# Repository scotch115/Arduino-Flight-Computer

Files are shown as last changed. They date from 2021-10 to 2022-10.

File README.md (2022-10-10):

# Arduino Telemetry

Arduino-based IMU telemetry system for model rockets. 

Phase 1: Build a basic Arduino project to learn basics of handling sensor data and developing on an MCU

Phase 2: Design and build a custom flight computer using accessible components and write flight-capable software.

Phase 3: Design and build a ground-control system to communicate with flight computer, handle launch sequence and startup, transmit data to and from the flight computer to a laptop.

Phase 4: Design and assemble the rocket airframe, mount the flight computer and Rotation Control System (RCS but not that kind ;P ), and test avionics and telemetry.

Phase 5: Build and test chute ejection system and determine required powder charge level.

Phase 6: Launch! 🚀

# Phase I - Research
## Temp Sensor PCB Design
### MK I
The MK I PCB was unfortunately unsuccessful, as I used the EasyEDA autoroute feature to try to solve track placement issues, however it did not take into account the possiblity of shorting the circuits, and neither did I, so my Arduino Nano blew a capacitor. Thankfully I have more, but this board was immediately decommissioned.

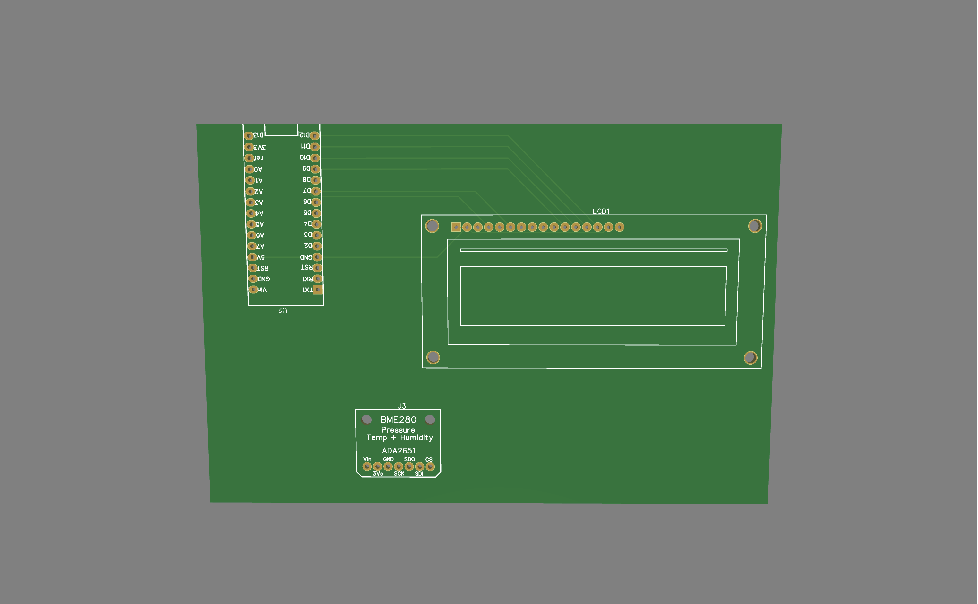
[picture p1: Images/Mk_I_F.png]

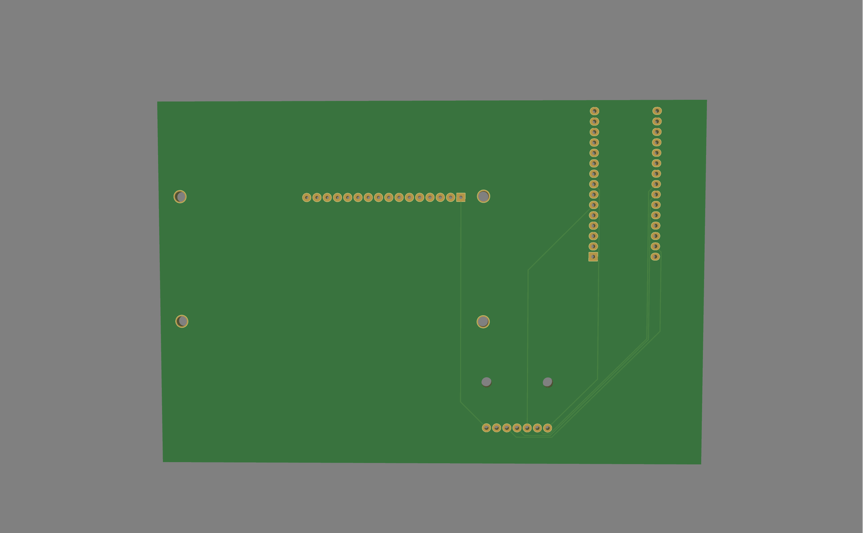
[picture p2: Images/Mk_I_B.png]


### MK II
The MK II PCB was carefully redesigned to improve upon the Mk I's failures by utilizing better component placement, built-in grounding pads, and hand-drawn track placement.

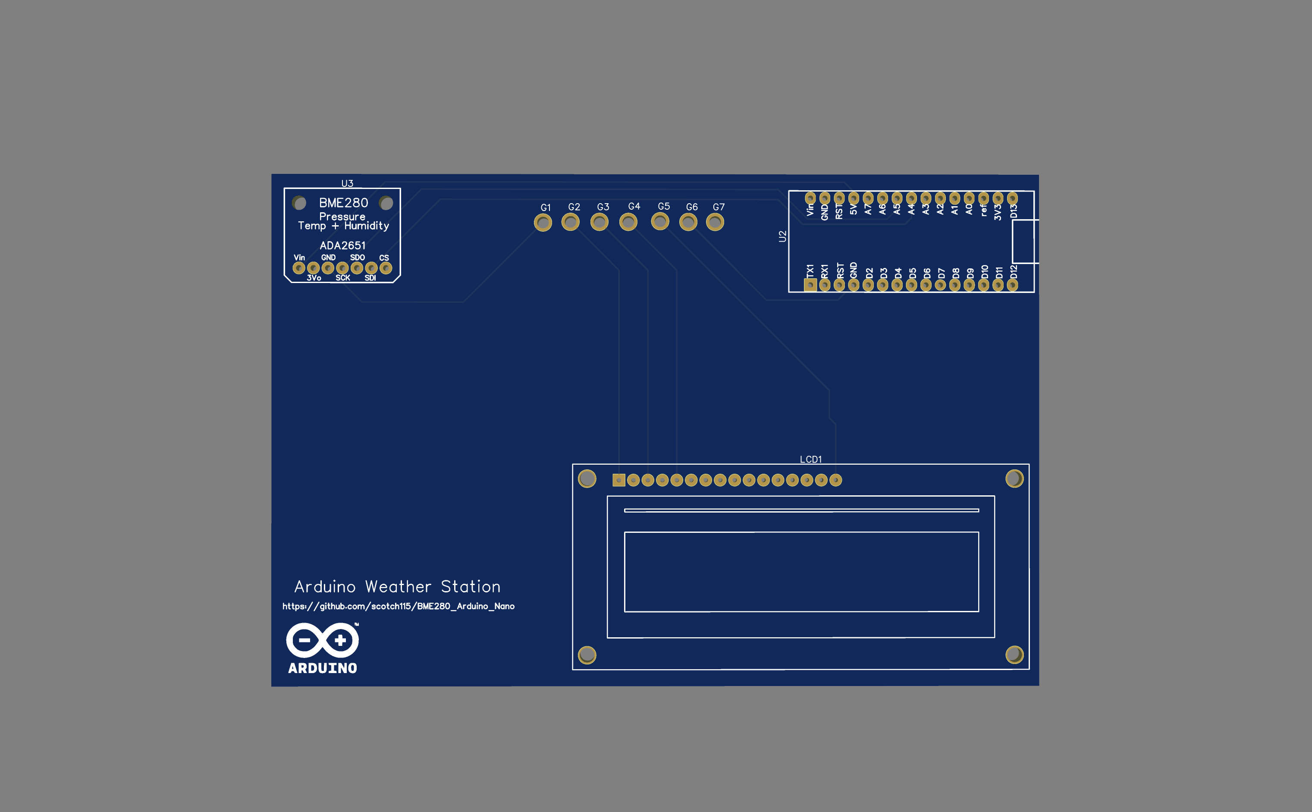
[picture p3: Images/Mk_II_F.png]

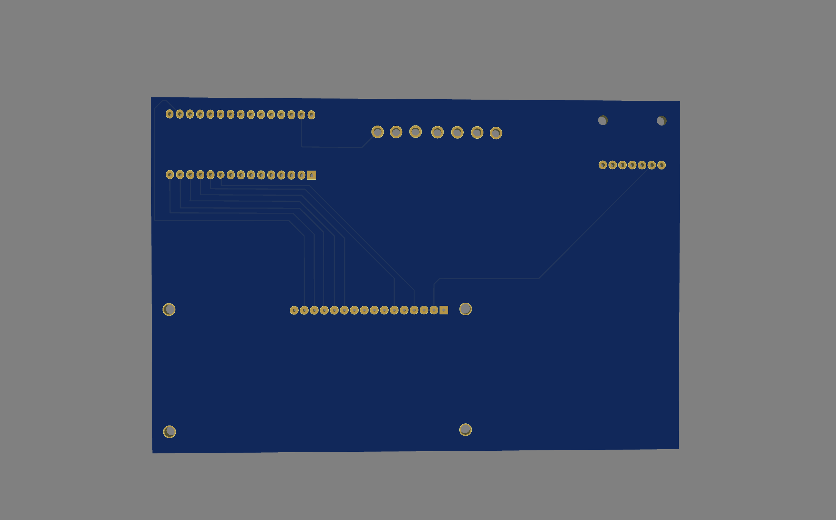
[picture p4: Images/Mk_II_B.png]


## Update:
Custom PCB worked after a slight modification to the electrical grounding system. Further research concluded that a "common ground" pin would have been more efficient and effective, than multiple pins.



# Phase II - Development
## Flight Computer
This is the assembled Mk.1 version of the flight computer, equipped with a barometer and IMU for tracking altitude, temperature, orientation, and velocity.




> UPDATE (MK. II)
>
> The flight computer has been upgraded to use the Adafruit Feather M0 with LoRa Radio @900Mhz, and the onboard IMU has been upgraded to the MPU 6050 with 6 DOF (and gyroscope!).

### MK.III
After working through various software iterations, the prototype board was complete and functional, but rather messy and utilized more patch wires than I preffered. Using the skills I learned from the PCB design in Phase 1, I began designing a new flight computer PCB, with the intent of using the same core components from the prototype board, allowing an easy transition of functionality, and requiring litte to no software logic changes. The Blep flight computer was developed, and serves as a major improvement in terms of efficiency, durability, and technological advancement. Having learned from my mistakes with the Phase 1 power management, I introduced a single common ground via on the PCB, as well as an entire "ground plane" within the layers of the PCB to ensure that all of the routes on the front and back of the board share a truly **common** ground.



# Phase III - Ground Control
## Mk. I
The AirLift Wi-Fi Co-Processor on both the Adalogger and Metro are able to successfully communicate with the Node-Red server, to send sensor data over UDP for collection and assimilation. The Node-Red dashboard is configured to not only build graphs in real-time, but also saves the data as it is received to a JSON file. 

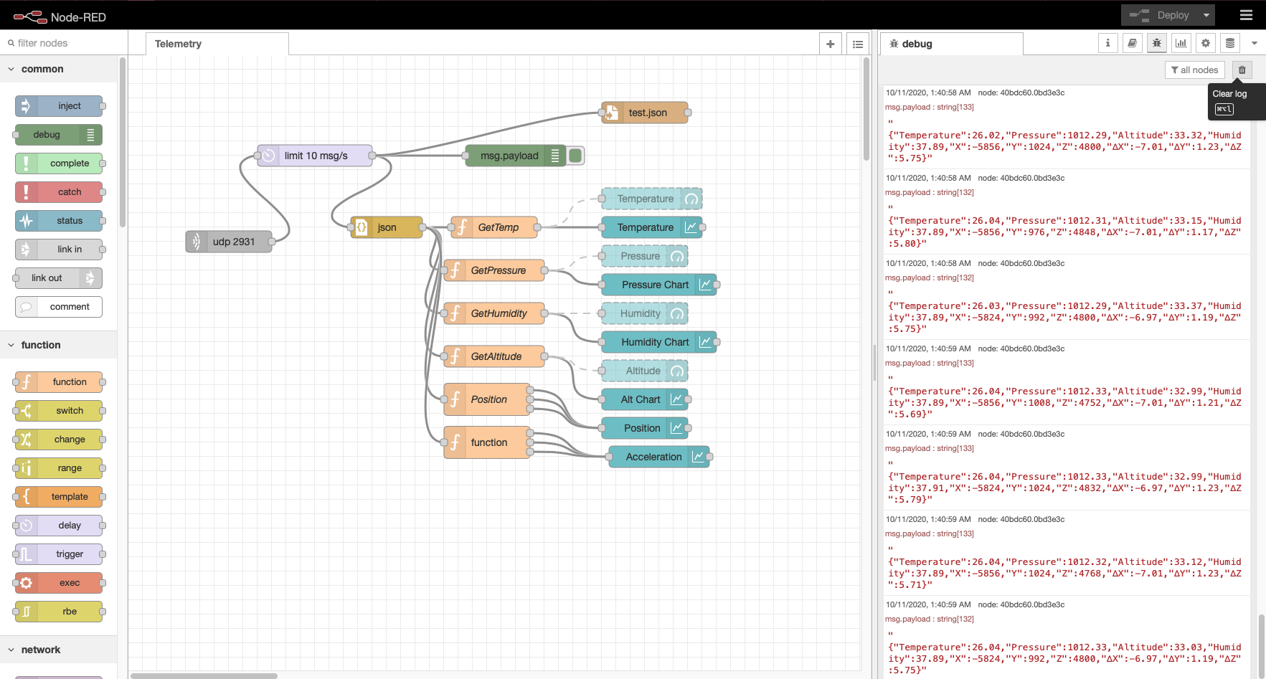
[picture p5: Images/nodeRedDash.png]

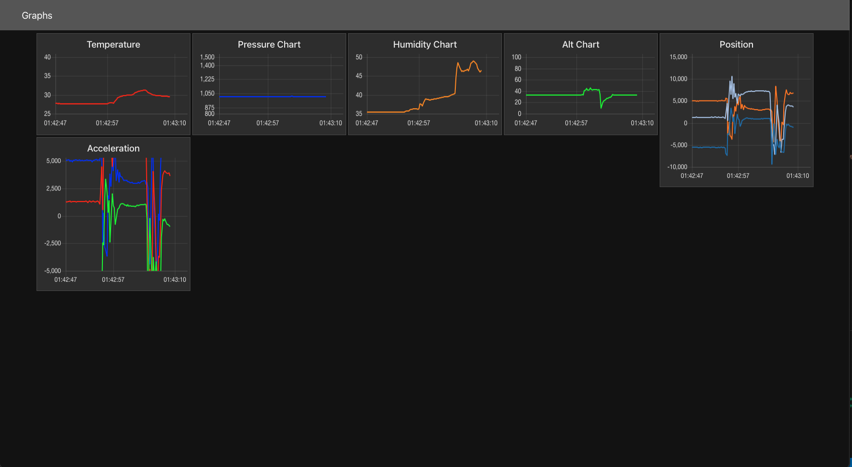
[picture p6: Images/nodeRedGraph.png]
  

## Mk. II
When the flight computer software is complete, the ground control system will be updated. Now that the onboard telemtry has shifted to use 900Mhz radio, the communication with the rocket will also be updated to use radio, and the data received by the ground control computer will be sent to a new server for analysis and logging. The new data analysis server utilizes Serial Studio instead of node-red, which is significantly more robust and efficient when dealing with high-speed data input, and doesn't suffer from the read/write operations to graphs, but still provides a JSON file as output for post-launch analysis. The primary MCU for the ground control computer will be a Teensy 3.2, connected to a LoRa Featherwing using the Teensy-Feather adapter board. 

# Phase IV - Rocket Design and Construction 
> ~~Currently doing research and teaching myself rocket mechanics to design and build a stable, efficient rocket.~~  
> UPDATE (9/2022): The rocket airframe is being designed simultaneous with Phase II, and rudimentary schematics will be included in this repo for future use. Old PCB schematics have been scrubbed from the project, as they are no longer relevant or necessary, and have been replaced by the Blep flight computer PCB files. Airframe construction will likely begin in the order planned.

# Phase V - Chute Ejection System
> Development still in progress...

# Phase VI - Launch!
> Development still in progress...

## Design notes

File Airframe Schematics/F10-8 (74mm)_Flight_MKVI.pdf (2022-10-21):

## Rocket Design

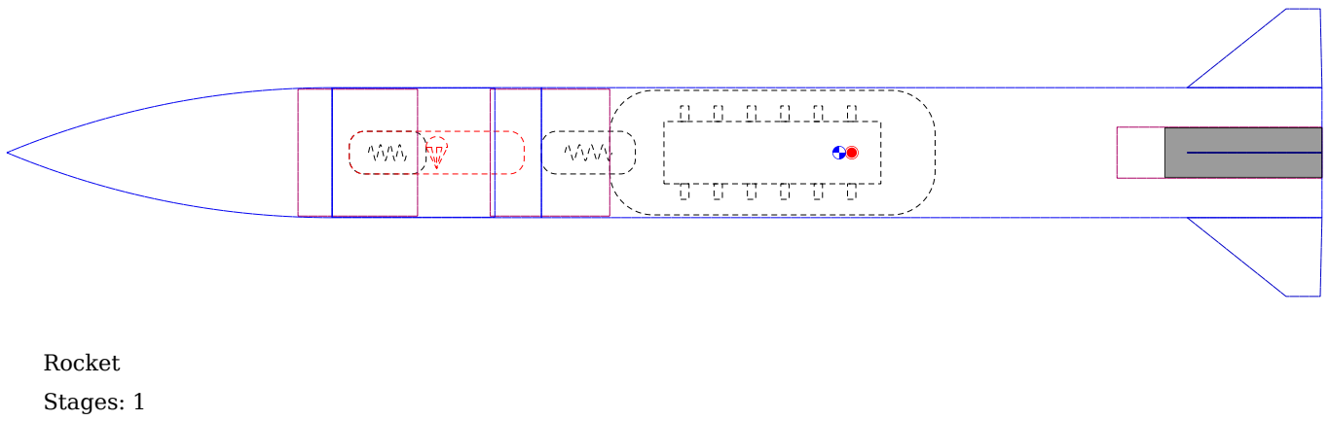
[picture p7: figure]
Rocket; Stages: 1

F10-8

Mass (with motor): 447 g

Stability: 0.097 cal

CG: 48.7 cm

CP: 49.5 cm

Altitude | 513 m
Flight Time | 60.1 s

Time to Apogee 12.2 s

Optimum Delay 5.1 s

Velocity off Pad 9.79 m/s

Max Velocity | 67.3 m/s
Velocity at Deployment | 3.26 m/s

Landing Velocity 10.7 m/s

Motor | Avg Thrust | Burn Time | Max Thrust | Total Impulse | Thrust to Wt | Motor Wt | Size
F10 | 10.9 N | 7.02 s | 28.2 N | 76.3 Ns | 2.48:1 | 40.7 g | 29/92 mm

## Parts Detail

Sustainer

Nose cone | [material:[mate
rial:polystyrene
PS]]

(1 g/cm³)

Ogive | Len: 19 cm | Mass: 92.7 g
Body tube | Cardboard

(0.68 g/cm³)

Diain 7.44 cm
Diaout 7.62 cm
| Len: 12.2 cm | Mass: 17.7 g
Tube coupler | Cardboard

(0.68 g/cm³)

Diain | 7.44 cm
Diaout 7.44 cm | Len: 7 cm | Mass: 0 g
Parachute | Ripstop nylon

(67 g/m²)

Diaout 30 cm | Len: 10.2 cm | Mass: 7.98 g
Shroud Lines | Elastic cord
(round 2 mm,
1/16 in)

(1.8 g/m)

Lines: 6 | Len: 30 cm
Shock cord | Kevlar thread
800 (1.1 mm,
3/64 in)

(0.992 g/m)

Len: 40 cm | Mass: 0.397 g
Body tube | Cardboard

(0.68 g/cm³)

Diain 7.44 cm
Diaout 7.62 cm
Len: 45.7 cm | Mass: 66.2 g
Tube coupler | Cardboard

(0.68 g/cm³)

Diain 7.44 cm
Diaout 7.44 cm
Len: 7 cm | Mass: 0 g
Flight Computer | Diaout 7.3 cm | Mass: 96 g
Inner Tube | Cardboard

(0.68 g/cm³)

Diain | 2.9 cm
| Diaout 2.99 cm
Len: 12 cm | Mass: 3.4 g
Trapezoidal fin set (4) | PLA

(1.25 g/cm³)

| Thick: 0.8 cm | Mass: 77.7 g
Shock cord | Kevlar thread
800 (1.1 mm,
3/64 in)

(0.992 g/m)

Len: 40 cm Mass: 0.397 g

## Trapezoidal fin set

## Trapezoidal fin set

## Trapezoidal fin set

## Trapezoidal fin set

## in cm

cm
in

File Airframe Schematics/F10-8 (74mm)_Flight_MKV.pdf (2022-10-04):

## Rocket Design

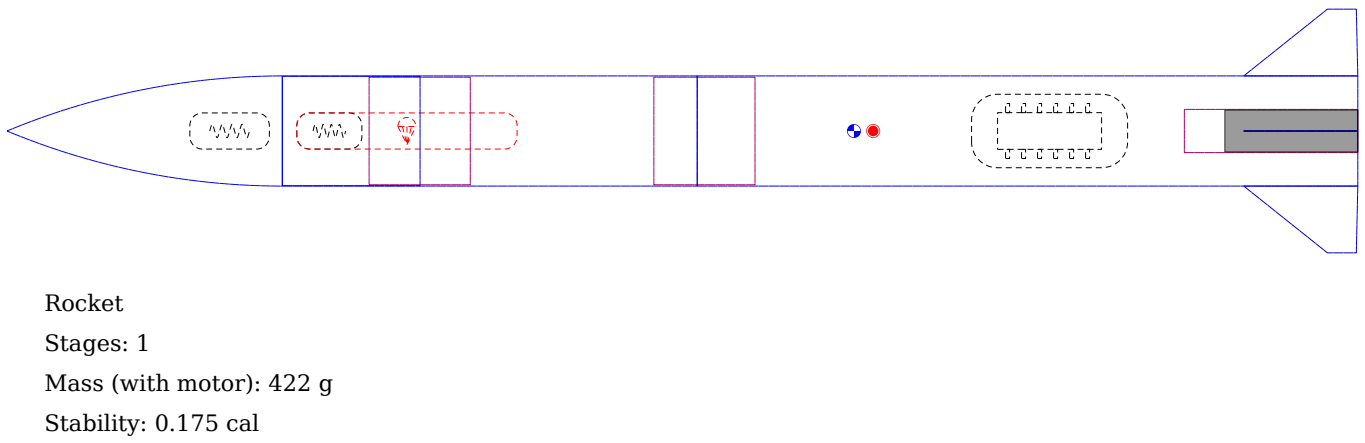
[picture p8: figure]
Rocket; Stages: 1; Mass (with motor): 422 g; Stability: 0.175 cal

F10-8

CG: 58.6 cm

CP: 59.9 cm

Altitude | 520 m
Flight Time | 62.2 s

Time to Apogee 12.1 s

Optimum Delay 5 s

Velocity off Pad 10.5 m/s

Max Velocity | 68.3 m/s
Velocity at Deployment | 5.24 m/s

Landing Velocity 10.4 m/s

Motor | Avg Thrust | Burn Time | Max Thrust | Total Impulse | Thrust to Wt | Motor Wt | Size
F10 | 10.9 N | 7.02 s | 28.2 N | 76.3 Ns | 2.62:1 | 40.7 g | 29/92 mm

## Parts Detail

Sustainer

Nose cone | [material:[mate
rial:polystyrene
PS]]

(1 g/cm³)

Ogive | Len: 19 cm | Mass: 92.7 g
Body tube | Cardboard

(0.68 g/cm³)

Diain 7.44 cm
Diaout 7.62 cm
| Len: 28.7 cm | Mass: 41.6 g
Tube coupler | Cardboard

(0.68 g/cm³)

Diain | 7.44 cm
Diaout 7.44 cm | Len: 7 cm | Mass: 0 g
Parachute | Ripstop nylon

(67 g/m²)

Diaout 30 cm | Len: 15.2 cm | Mass: 7.98 g
Shroud Lines | Elastic cord
(round 2 mm,
1/16 in)

(1.8 g/m)

Lines: 6 | Len: 30 cm
Shock cord | Elastic cord
(round 2 mm,
1/16 in)

(1.8 g/m)

Len: 40 cm | Mass: 0.72 g
Body tube | Cardboard

(0.68 g/cm³)

Diain 7.44 cm
Diaout 7.62 cm
Len: 45.7 cm | Mass: 66.2 g
Tube coupler | Cardboard

(0.68 g/cm³)

Diain 7.44 cm
Diaout 7.44 cm
Len: 7 cm | Mass: 0 g
Flight Computer | Diaout 5.08 cm | Mass: 96 g
Inner Tube | Cardboard

(0.68 g/cm³)

Diain | 2.9 cm
| Diaout 2.99 cm
Len: 12 cm | Mass: 3.4 g
Trapezoidal fin set (4) | PLA

(1.25 g/cm³)

| Thick: 0.3 cm | Mass: 29.1 g
Shock cord | Elastic cord
(round 2 mm,
1/16 in)

(1.8 g/m)

Len: 40 cm Mass: 0.72 g

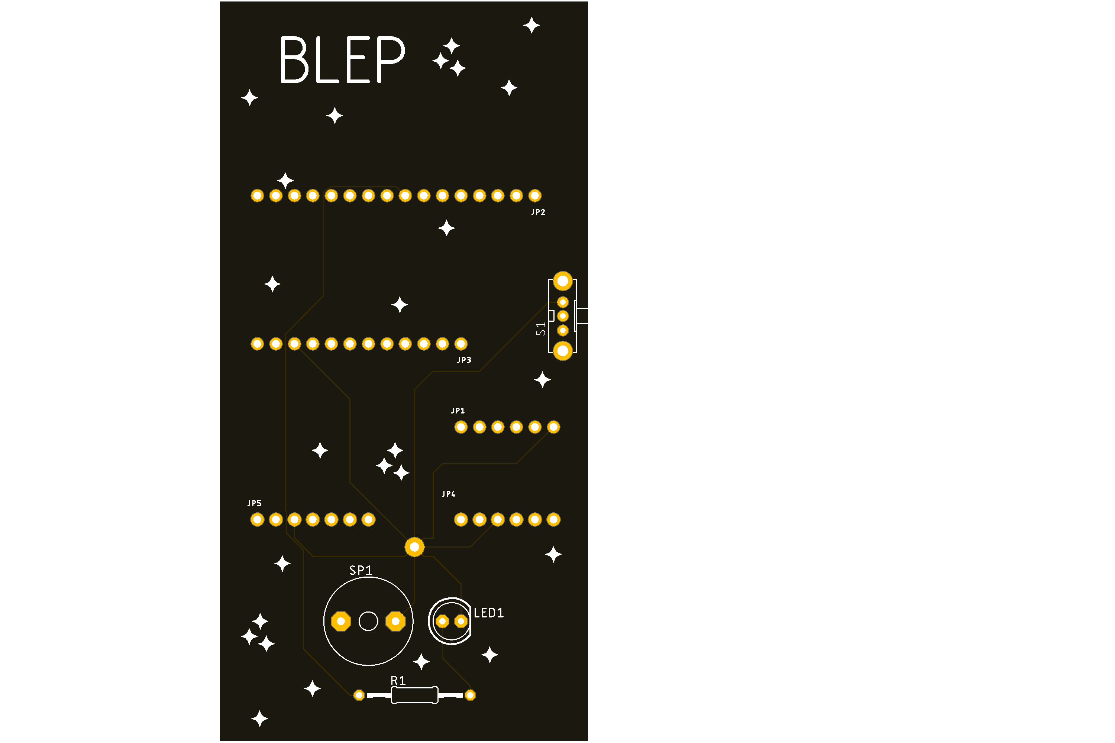
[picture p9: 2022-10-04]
Schematics/PCB Design Files/FlightComputer-PCB.png

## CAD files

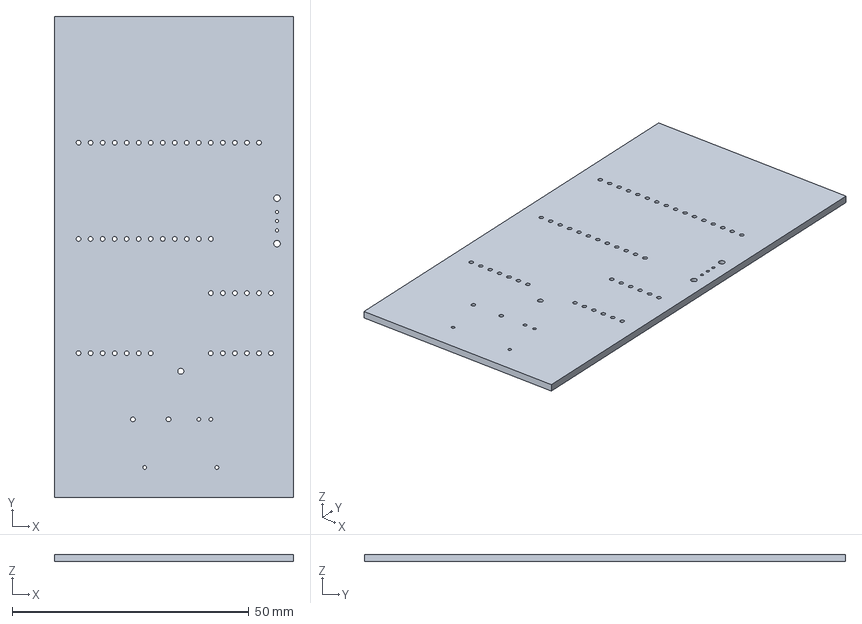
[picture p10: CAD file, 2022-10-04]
Schematics/PCB Design Files/FlightComputer v6.step
50.5 x 101.6 x 1.57 mm

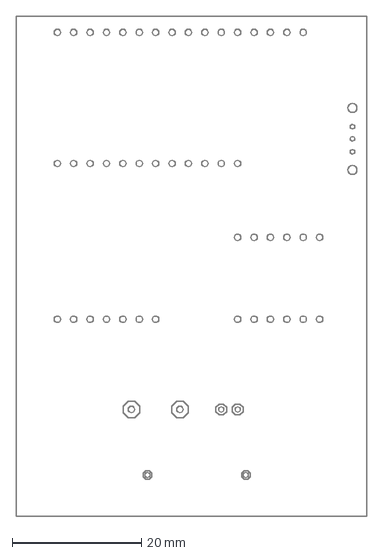
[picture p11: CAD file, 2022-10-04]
Schematics/PCB Design Files/FlightComputer.dxf
54.3 x 77.5 mm

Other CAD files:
Schematics/Technical Drawings/Servo Mount.dwg
Schematics/Technical Drawings/Avionics Payload Mount.dwg
Schematics/Technical Drawings/Sled Plate.dwg

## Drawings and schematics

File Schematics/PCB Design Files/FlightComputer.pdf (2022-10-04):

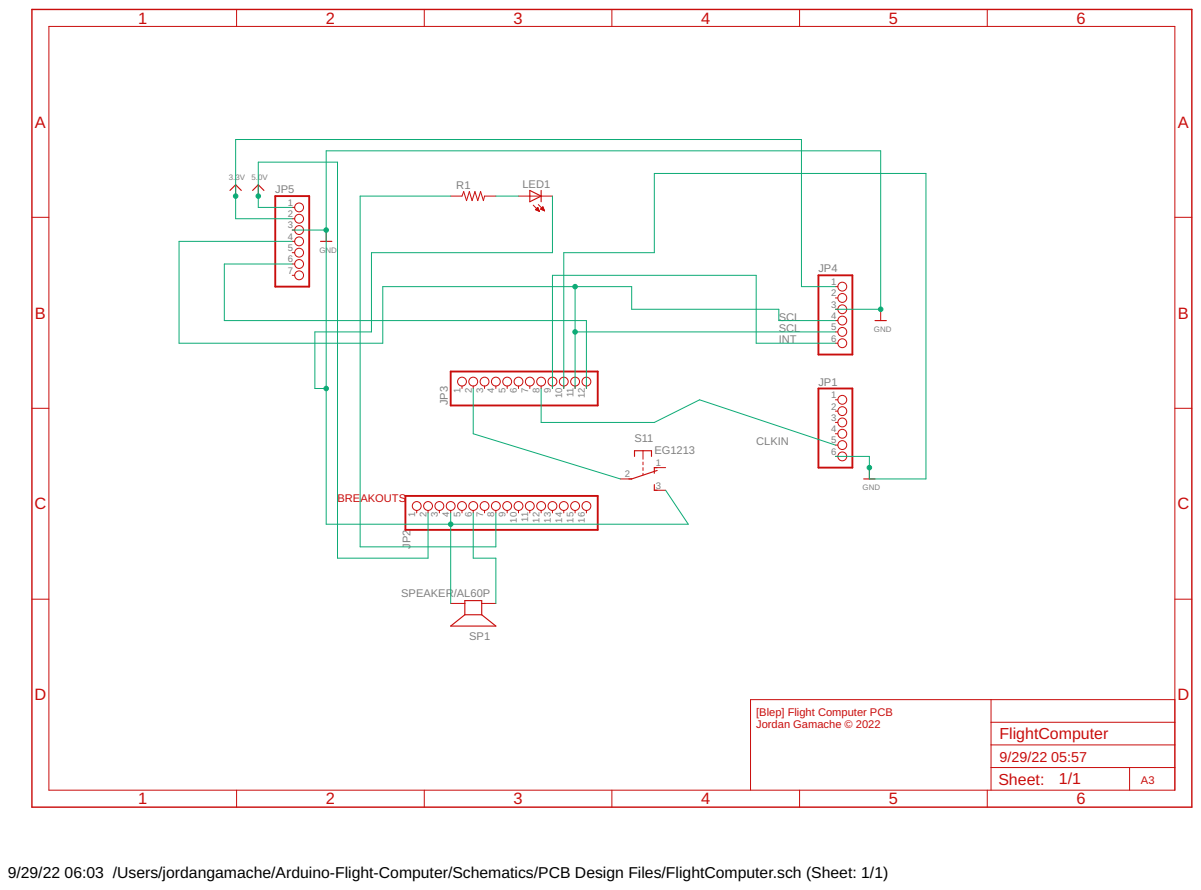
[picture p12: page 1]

[Blep] Flight Computer PCB Jordan Gamache © 2022

Sheet: 1/1 | A3

9/29/22 06:03 /Users/jordangamache/Arduino-Flight-Computer/Schematics/PCB Design Files/FlightComputer.sch (Sheet: 1/1)

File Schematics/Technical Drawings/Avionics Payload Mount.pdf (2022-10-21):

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

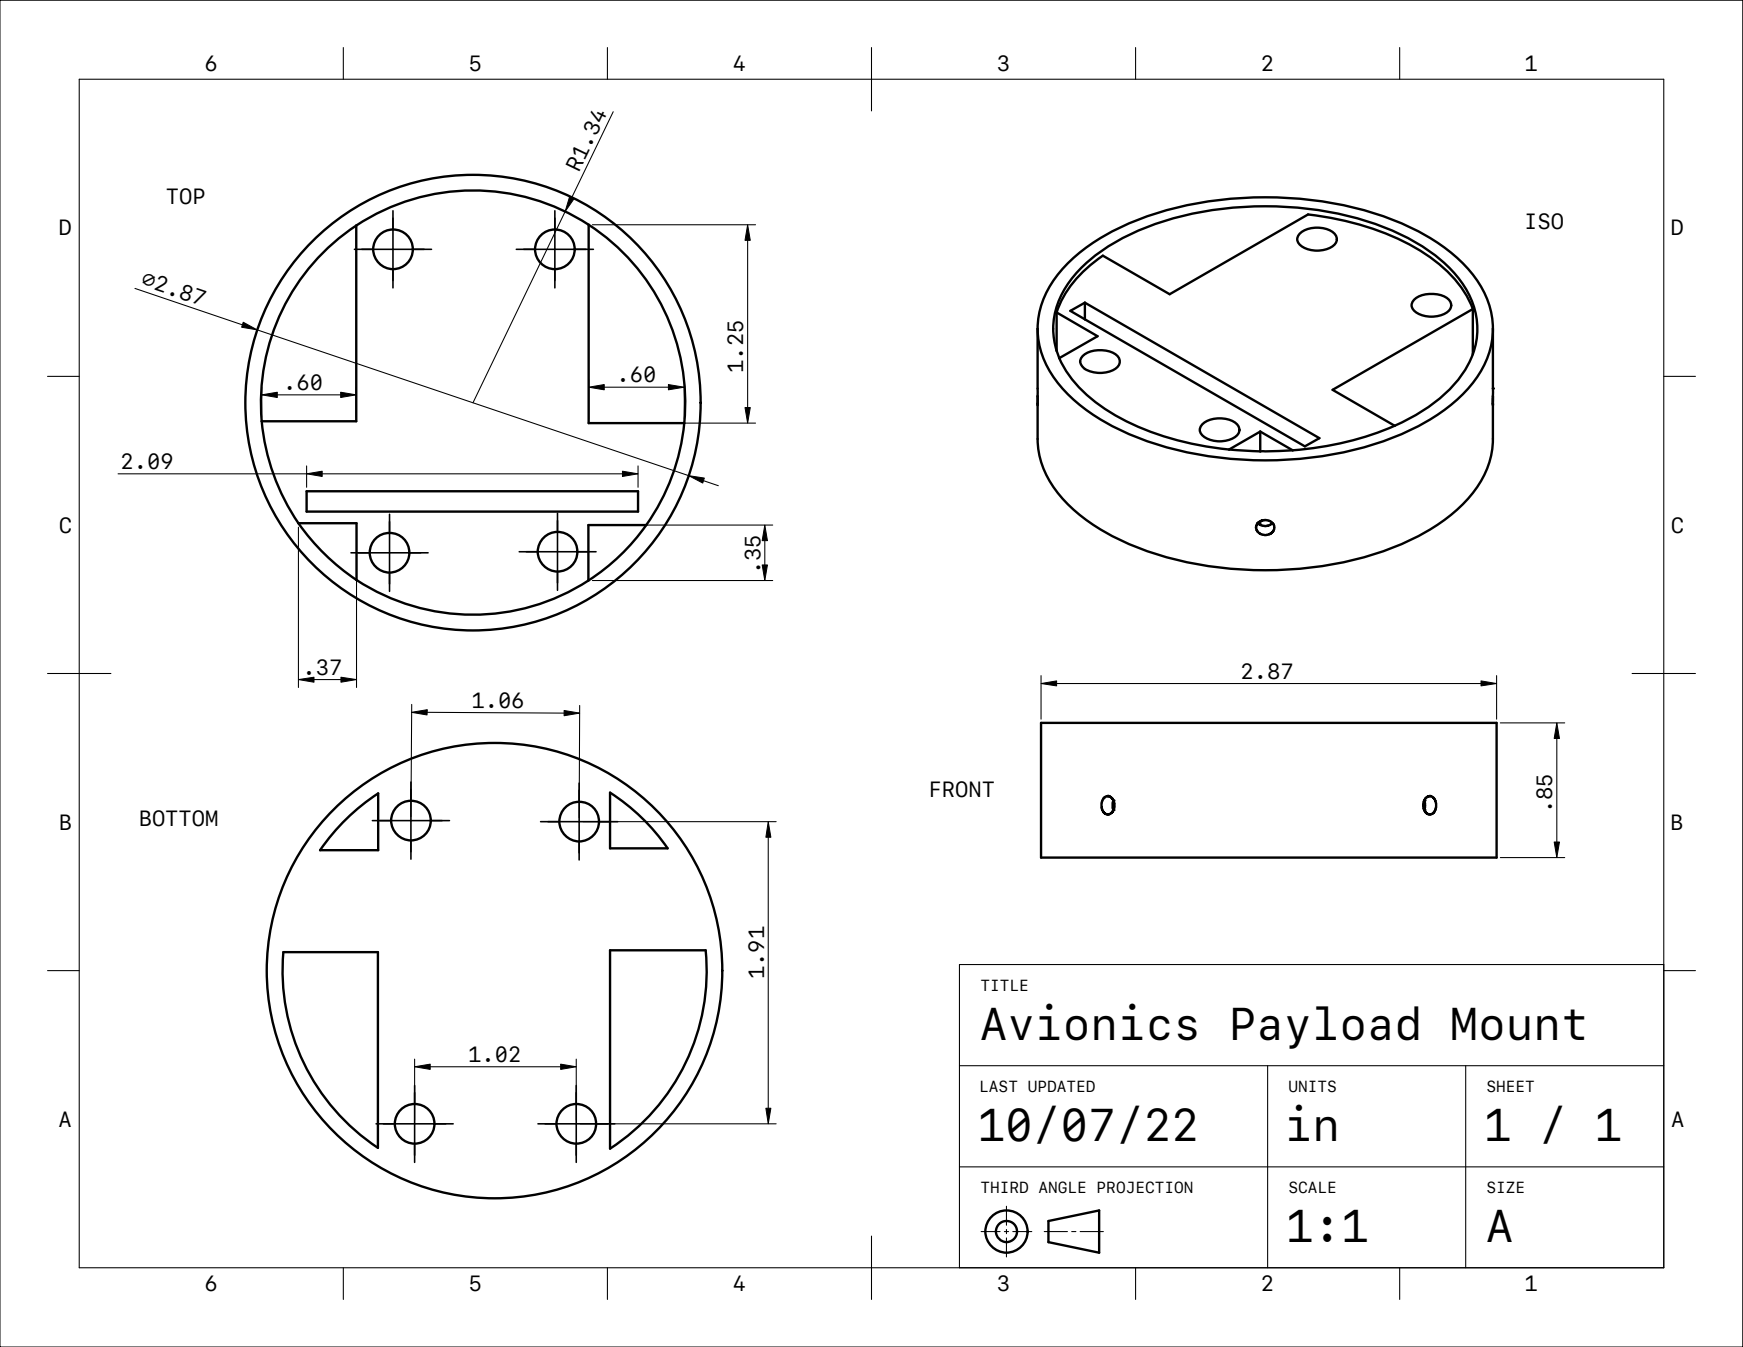
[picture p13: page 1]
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

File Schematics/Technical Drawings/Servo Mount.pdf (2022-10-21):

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

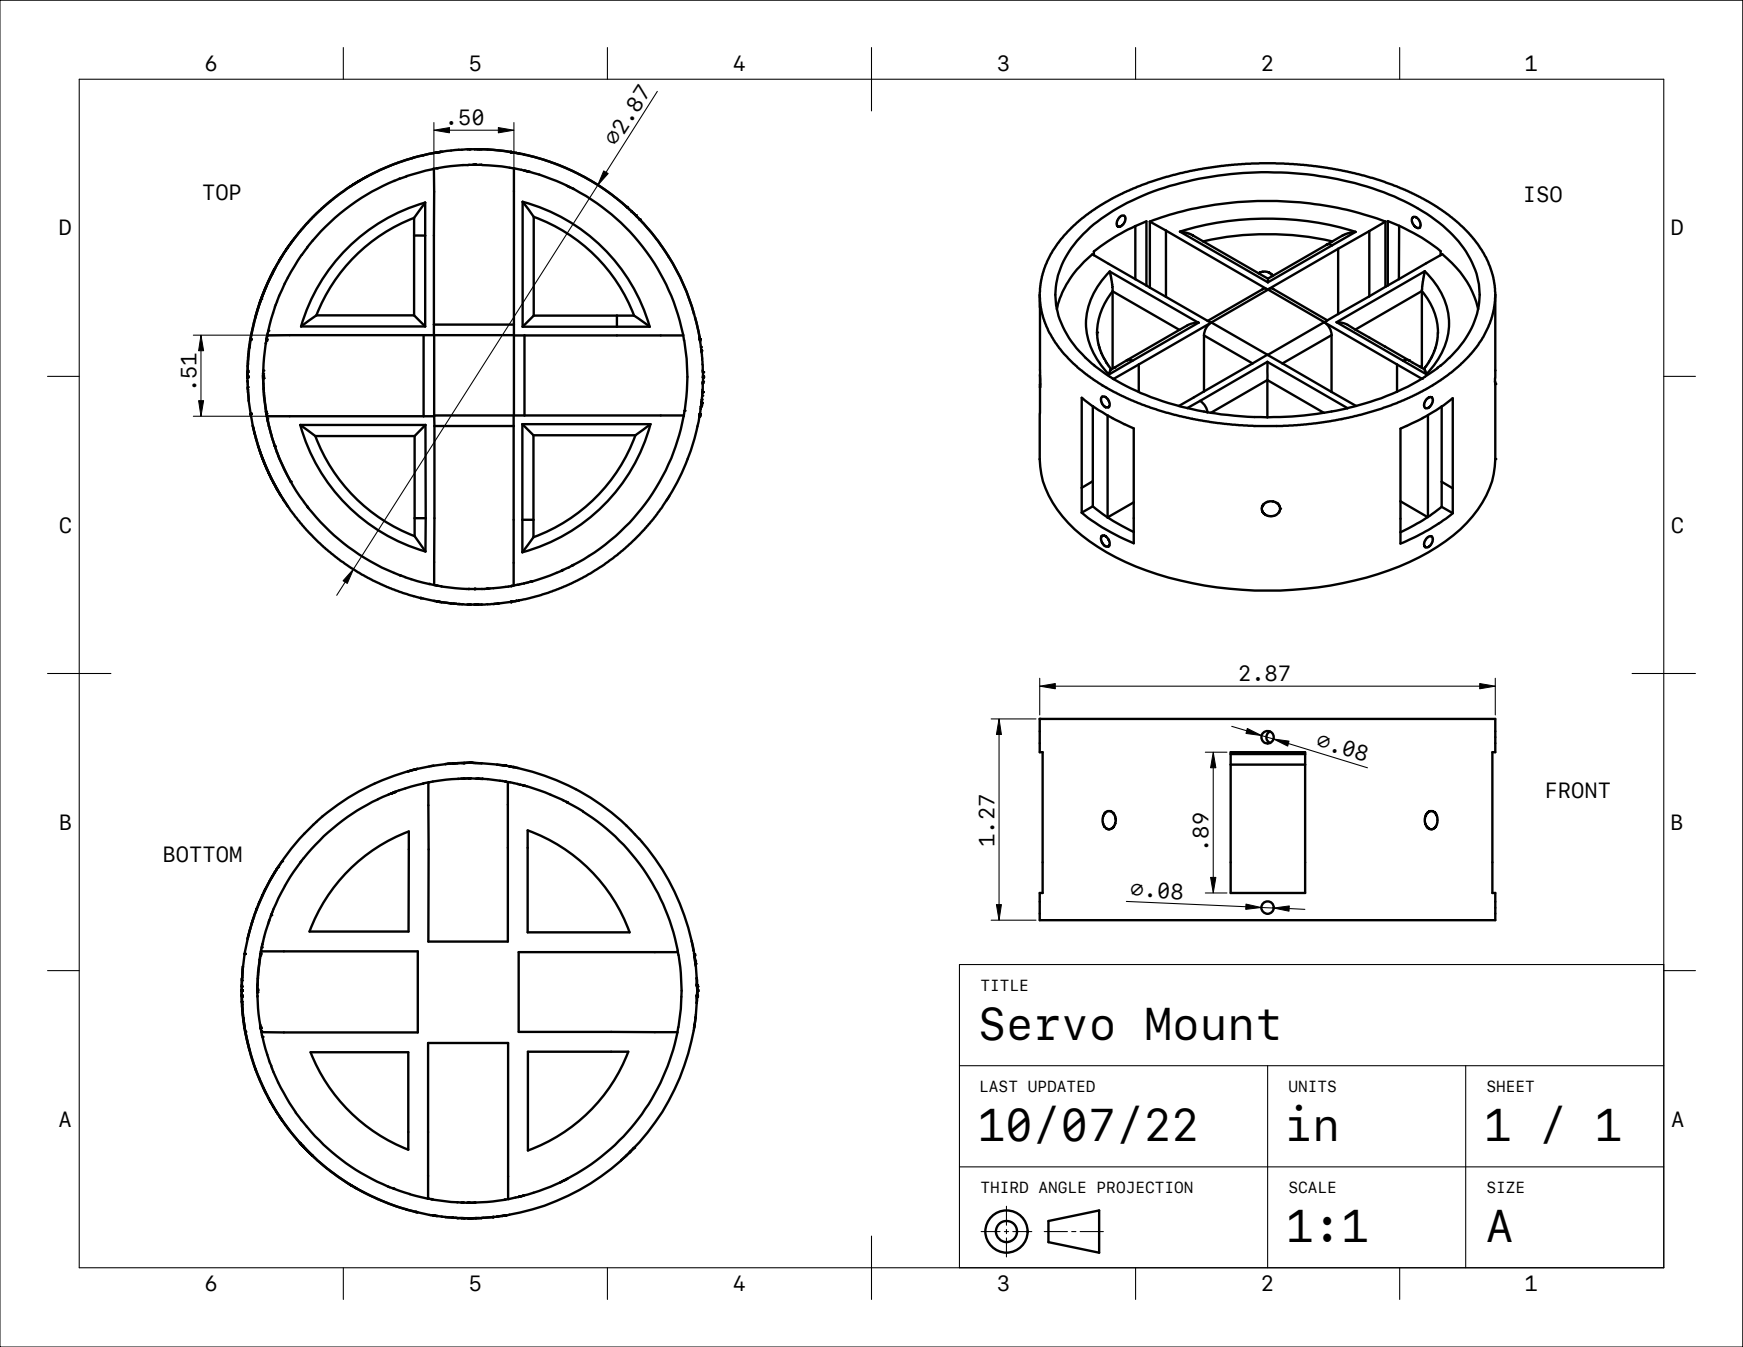
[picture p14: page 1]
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

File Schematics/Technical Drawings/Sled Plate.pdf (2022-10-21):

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

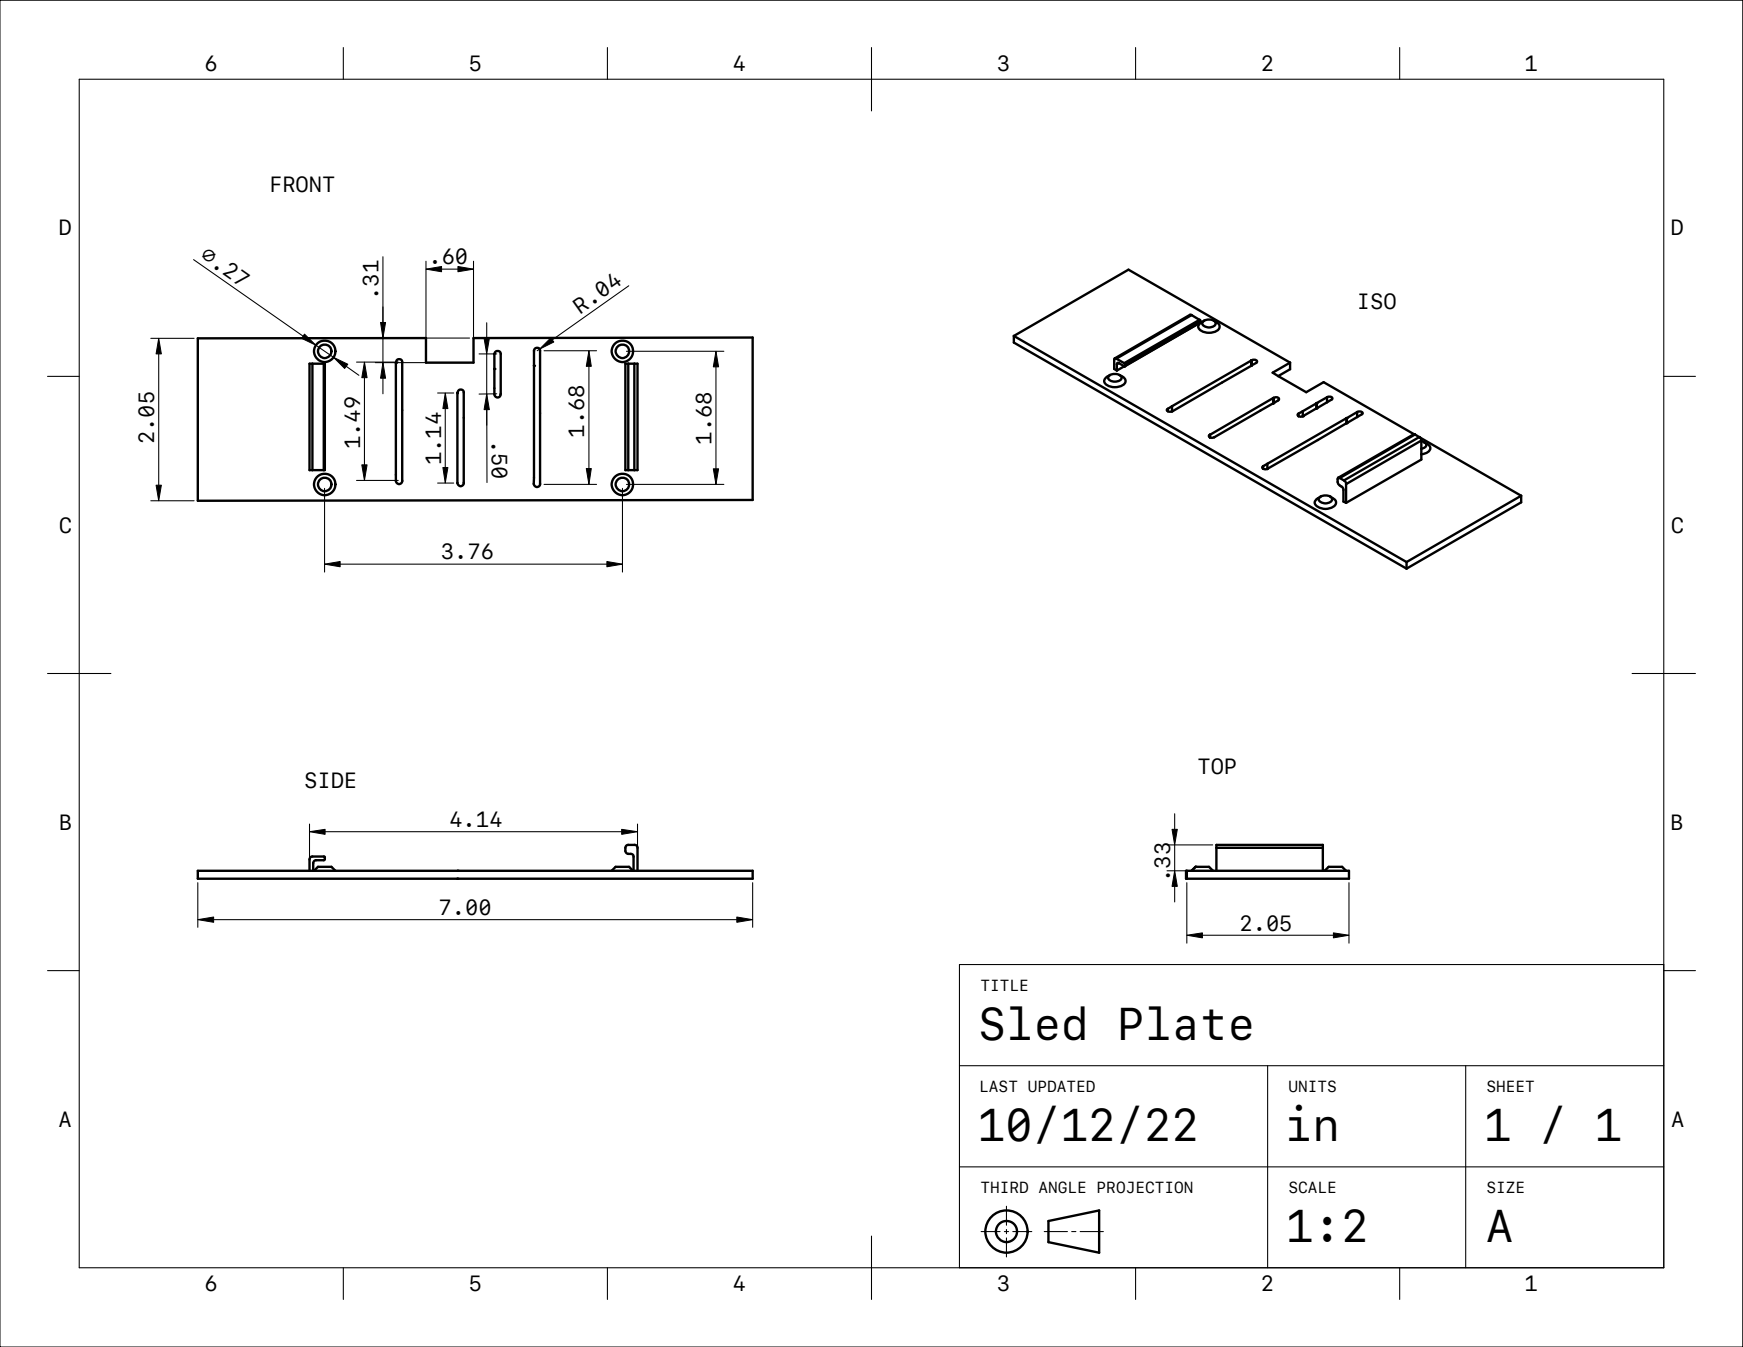
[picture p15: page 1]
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

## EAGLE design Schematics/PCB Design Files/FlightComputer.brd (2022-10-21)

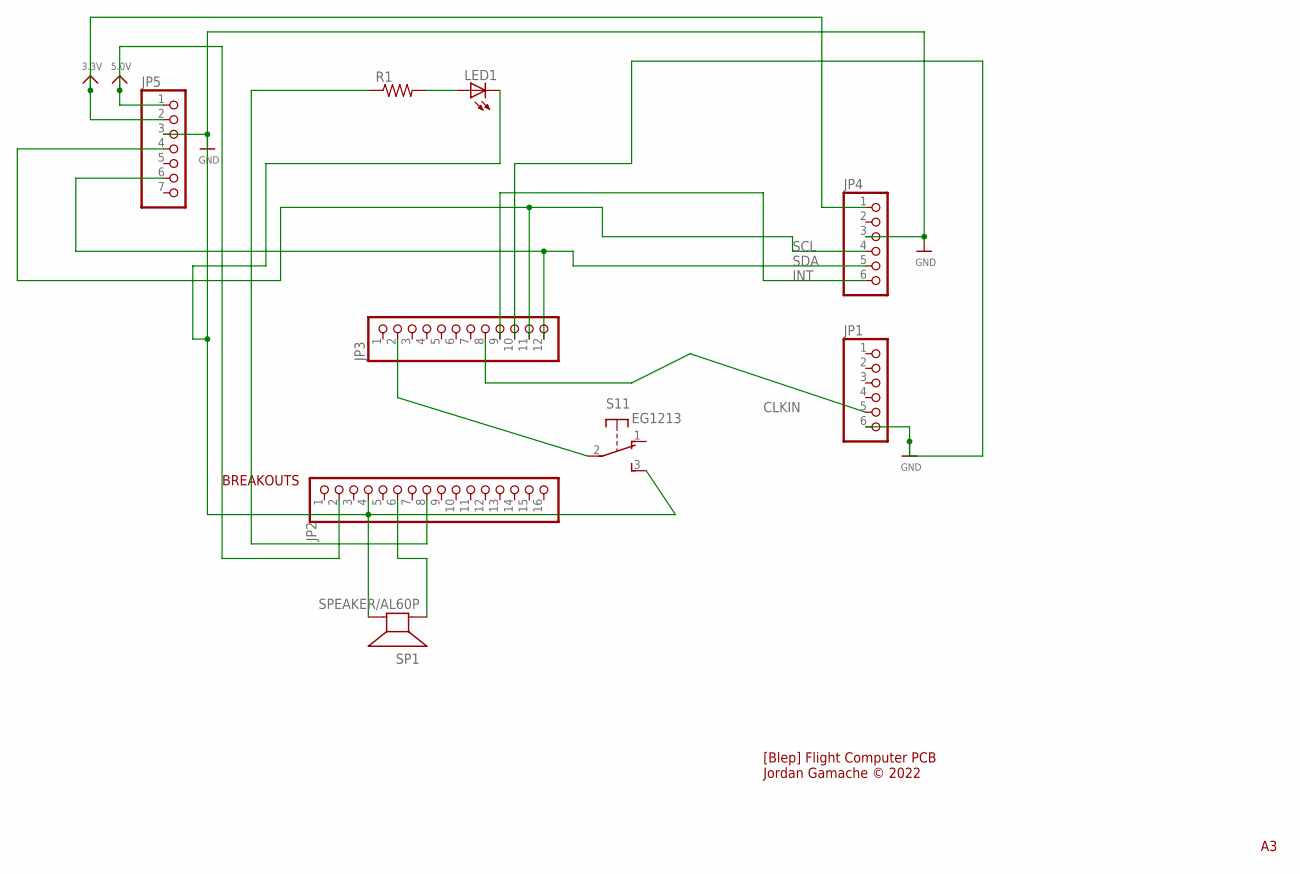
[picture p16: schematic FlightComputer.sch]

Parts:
JP1: HEADER-1X6ROUND; 1X06_ROUND
JP2: HEADER-1X16ROUND; 1X16_ROUND
JP3: HEADER-1X12; 1X12_ROUND
JP4: HEADER-1X670MIL; 1X06_ROUND_70
JP5: HEADER-1X770MIL; 1X07_ROUND_70
LED1: LED5MM
R1: R-US_0207/15; 0207/15
S1: EG1213
SP1: SPEAKER/AL60P; AL60P

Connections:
3.3V: JP4.1, JP5.2
5.0V: JP2.2, JP5.1
CLKIN: JP1.5, JP3.8
GND: JP1.6, JP2.4, JP3.10, JP4.3, JP5.3, LED1.K (C), S1.3 (S), SP1.2 (-)
INT: JP3.9, JP4.6
unnamed: JP2.6, SP1.1 (+)
unnamed: JP2.8, R1.1
unnamed: LED1.A, R1.2
unnamed: JP3.2, S1.2
SCL: JP3.11, JP4.4, JP5.4
SDA: JP3.12, JP4.5, JP5.6

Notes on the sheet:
BREAKOUTS
[Blep] Flight Computer PCB Jordan Gamache © 2022

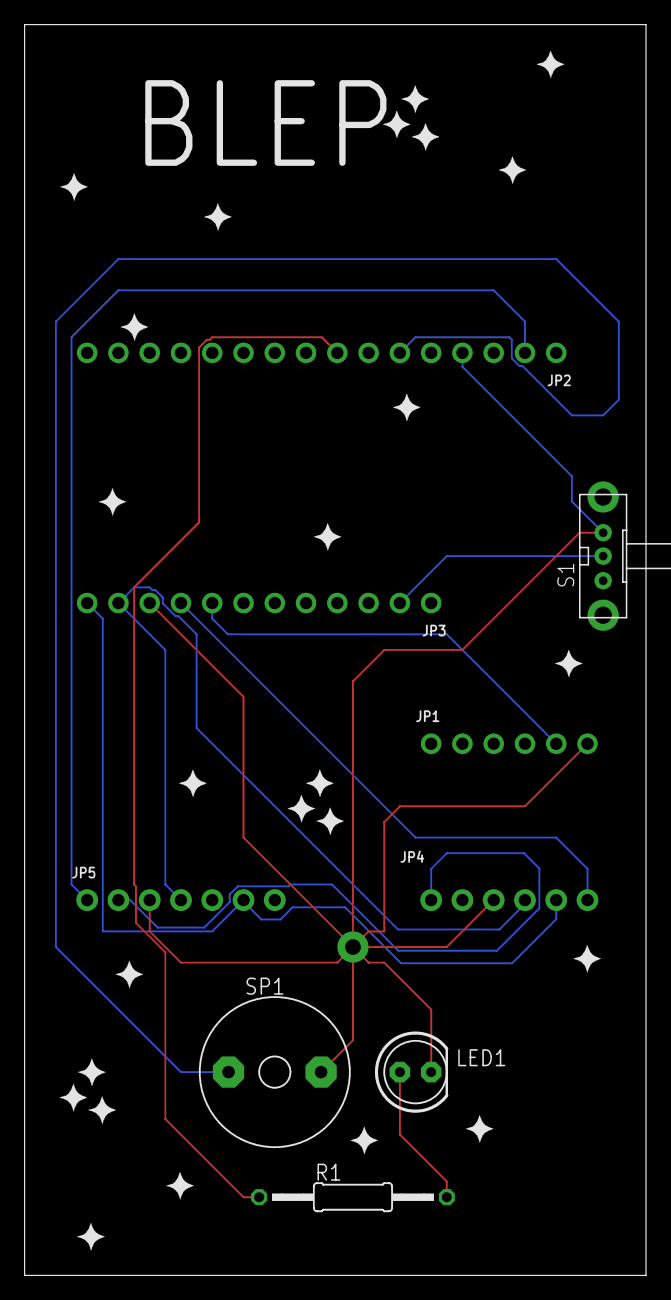
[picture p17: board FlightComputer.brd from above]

Board: 2 copper layers, 50.5 x 101.6 mm, 9 parts (0 on the bottom side), 11 nets.

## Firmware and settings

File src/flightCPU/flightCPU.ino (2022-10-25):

#include <Servo.h>
#include "Wire.h"
#include <SPI.h>
#include <Adafruit_Sensor.h>
#include <Adafruit_BME280.h>
#include "I2Cdev.h"
#include "MPU6050_6Axis_MotionApps612.h"
#include <RH_RF95.h>
#include <avr/dtostrf.h>
#include <SimpleKalmanFilter.h>
#include "variables.h"
#include "flightConfiguration.h"

/****************************************************************************************************************************************************************************/
/****************************************************************************************************************************************************************************/
/****************************************************************************************** Startup *************************************************************************/
/****************************************************************************************************************************************************************************/
/****************************************************************************************************************************************************************************/

void setup() {
  // join I2C bus (I2Cdev library doesn't do this automatically)
    #if I2CDEV_IMPLEMENTATION == I2CDEV_ARDUINO_WIRE
      Wire.begin();
      Wire.setClock(400000); // 400kHz I2C clock. Comment this line if having compilation difficulties
    #elif I2CDEV_IMPLEMENTATION == I2CDEV_BUILTIN_FASTWIRE
      Fastwire::setup(400, true);
    #endif

  /*   Prep RMF95 for flight   */
  if (TELEMETRY == "ACTIVE") {
    pinMode(RFM95_RST, OUTPUT);
    digitalWrite(RFM95_RST, HIGH);
  }
  
  Serial.begin(115200);

  // Wait for serial to be available if board is in 'DEBUG' mode
  if (debugState == "ON") {
    while (!Serial) {
    }
  }

  // Run pre-flight check
  preCheck();
}

/*****************************************************************************************************************************************************************************/
/*****************************************************************************************************************************************************************************/
/************************************************************************* flightControl loop *********************************************************************************/
/*****************************************************************************************************************************************************************************/
/*****************************************************************************************************************************************************************************/

void loop() {
/**
 * @note - The flight CPU should have the following states, some 
 * of which are receivable via 900mHz radio from the launch pad controller
 * 
 * @param - STARTUP
 * @param - STANDBY
 * @param - IDLE
 * @param - ARMED
 * @param - START CAMERA
 * @param - STOP CAMERA
 * @param - LIFTOFF
 * @param - CHUTE
 * @param - ERROR
 * @param - REBOOT
 * @param - TOUCHDOWN
 * @param - DEBUG
 */
  if (launchState == "ARMED"
  || launchState == "STANDBY") {
    missionBlep(interval, 1200);
    flightControl();
    if (TELEMETRY == "ACTIVE") {
      // Check to see if groundControl is available
      sync();
    }
    // Reduce power consumption of loop frequency by limiting data collection to 2Hz
    delay(500);
   } else if (launchState == "IDLE") {
    missionBlep(interval, 1000);
    flightControl();
    if (TELEMETRY == "ACTIVE") {
      // Check to see if groundControl is available
      sync();
    }
    // If flight computer is in 'IDLE' mode, lower to 0.3Hz to further improve battery performance
    delay(3000);
   } else if (launchState == "LIFTOFF"
   || launchState == "FLIGHT"
   || launchState == "CHUTE") {
    /**
     * Blep once every second to indicate that the flight computer is armed and ready
     */
    unsigned long missionTime = millis();
    // Blep twice as in flight to indicate a change in state
    missionBlep((interval / 2), 1200);
    flightControl();
  } else if (launchState == "REBOOT") {
    preCheck();
  } else if (launchState =="STARTUP") {
    return;
  } else if (launchState == "ERROR") {
    /**
     * Crash the program and force engineer(s) to follow standard operating procedures
     * and power down rocket for safety
     * */
    Serial.println("ERROR ERROR ERROR ERROR ERROR ERROR ERROR ERROR ERROR ERROR");
    Serial.println("!!!!! POWER DOWN THE ROCKET AND BE SURE TO DISENGAGE THE MOTOR !!!!!");
    Serial.println("!!!!! EVALUATE FLIGHT COMPUTER AND CIRCUITRY BEFORE CONTINUING !!!!!");
    Serial.println("!!!!! ENSURE CONTINUITY ON ALL COMPONENTS BEFORE ATTEMPTING FLIGHT !!!!!");
    Serial.println("ERROR ERROR ERROR ERROR ERROR ERROR ERROR ERROR ERROR ERROR");
    blep(BUZZER_PIN, 311, 1000);

    delay(10000);
  } else if (launchState == "TOUCHDOWN") {
    /* Play a deep, drone note */
    tone(BUZZER_PIN, 300);
    /* Beep periodically to help recovery crew find vehicle */
    blep(BUZZER_PIN, 523, 100);
  } else if (launchState == "DEBUG") {
    /* Do not limit data stream for efficient debugging */
    missionBlep(interval, 1200);
    flightControl();
  }
}

/******************************************************************/
/****************** Main In-Flight Control Logic ******************/
/******************************************************************/
void flightControl() {
  if (!dmpReady) return;
    if (mpu.dmpGetCurrentFIFOPacket(fifoBuffer)) {
      mpu.dmpGetQuaternion(&q, fifoBuffer);
      mpu.dmpGetGravity(&gravity, &q);
      mpu.dmpGetYawPitchRoll(ypr, &q, &gravity);
      mpu.dmpGetAccel(&aa, fifoBuffer);
      mpu.dmpGetLinearAccel(&aaReal, &aa, &gravity);

      /**
       * (WIP) *
       * Rocket camera feed will be handled by raspberry pi zero,
       * using a configuration similar to what is outlined here:
       * https://automaticaddison.com/2-way-communication-between-raspberry-pi-and-arduino/
       * 
       * The only expected obstacle at this time is going to be streaming the video to the ground computer,
       * because I don't think sending video signals over radio is going to be a good idea (or work at all).
       */

      
      /*************************************************
       * (WIP) *
       *  Check if rocket has reached or passed apogee * 
       *************************************************/
      getVehicleAltitude();

      if (chutesFired) {
        touchdown();
      }

      /******************************************************
       * Calculate Reaction Control offsets using IMU data, *
       * and pass values to servos to correct flight         *
       ******************************************************/
      if (RCS) {
        rcs(ypr);
      }

      /***************************************
       *    ? Get current battery level ?
       * ! REMOVE WHEN BATTERY IS UNPLUGGED  !
       **************************************/
      // Get current battery level
      // float measuredvbat = analogRead(VBATPIN);
      // measuredvbat *= 2;
      // measuredvbat *= 3.3;
      // measuredvbat /= 1024;

      transmitData();
    } 
} 

/***********************************************************************************************/
/********************************* Pre-Flight Startup Sequence *********************************/
/***********************************************************************************************/
void preCheck() {
  Serial.println();Serial.println();
  Serial.println("Beginning Pre-Flight Software check.");
  Serial.println();Serial.println();
  delay(2000);

  launchState = "STARTUP";
  Serial.println();
  Serial.print("Flight Computer Status: ");Serial.println(launchState);

  pinMode(LEDPIN, OUTPUT);

  // Play bootup sequence sound
  for (unsigned int i = 0; i < numTones; i++) {
    tone(BUZZER_PIN, tones[i]);
    delay(50);
  }
  noTone(BUZZER_PIN);
  delay(2000);  // time to get serial running
  unsigned status;

  /**********************************
   *     ? Boot up LoRa module ?
   * ! REMOVE WHEN TESTING OFFLINE  !
   **********************************/
  if (TELEMETRY == "ACTIVE") {
    Serial.println();
    Serial.println("LoRa Radio module found!");

    // Reset LoRa Module
    digitalWrite(RFM95_RST, LOW);
    delay(10);
    digitalWrite(RFM95_RST, HIGH);
    delay(10);

    while (!rf95.init()) {
      Serial.println("LoRa radio init failed");
      Serial.println("Uncomment '#define SERIAL_DEBUG' in RH_RF95.cpp for detailed debug info");
      while (1);
    }
    Serial.println("LoRa radio initialized!");

    if (!rf95.setFrequency(RF95_FREQ)) {
      Serial.println("setFrequency failed");
      while (1);
    }
    Serial.print("Frequency set to: "); Serial.println(RF95_FREQ);

    rf95.setTxPower(23, false);
  }

  Serial.println("First let's see if the BME280 Barometer is connected. Standby...");
 

  // Initialize and test BME 280
  status = bme.begin();
  if (!status) {
    Serial.println("Could not find a valid BME280 sensor, check wiring, address, sensor ID!");
    launchState = "ERROR";
  } else {
    if (status) {
      String bmeMsg = "Found the BME280 sensor! Here's some data...";
      char bMessage[200];
      int b = 0;
      while((b<200)) {
        bMessage[b]=bmeMsg[b];  
        b++;
      }

      Serial.println(bMessage);
      delay(2000);

      blep(BUZZER_PIN, 523, 50);

      Serial.print("Temperature = ");Serial.print(bme.readTemperature());Serial.println(" *C");
      Serial.print("Pressure = ");Serial.print((bme.readPressure() / 100.0F));Serial.println(" Pa");
      Serial.print("Approx Altitude = ");Serial.print(bme.readAltitude(SEALEVELPRESSURE_HPA));Serial.println(" m");
      Serial.print("Humidity = ");Serial.print(bme.readHumidity());Serial.println(" %");
      Serial.println();Serial.println();

      /**********************************
       * ? Send status update over LoRa ?
       * ! REMOVE WHEN TESTING OFFLINE  !
       **********************************/
      if (TELEMETRY == "ACTIVE") {
        rf95.send((uint8_t *)bMessage, 200);
        delay(10);
        rf95.waitPacketSent();
      }
    }
  }

  Serial.println("Now we'll look for the MPU6050 IMU. Standby...");
  
  delay(2000);
  
  // Initialize and test IMU (MPU 6050)
  mpu.initialize();
  pinMode(INTERRUPT_PIN, INPUT);
  String mpuMsg = "Found it! MPU6050 Connection Successful.";
  char mMessage[200];
  int m = 0;
  while((m<200)) {
    mMessage[m]=mpuMsg[m];  
    m++;
  }

  Serial.println(mMessage);

  /**********************************
   * ? Send status update over LoRa ?
   * ! REMOVE WHEN TESTING OFFLINE  !
   **********************************/
  if (TELEMETRY == "ACTIVE") {
    rf95.send((uint8_t *)mMessage, 200);
    delay(10);
    rf95.waitPacketSent();
  }

  devStatus = mpu.dmpInitialize();


  /*******************************
   * ! May require recalibration *
   *******************************/
    mpu.setXAccelOffset(XACCELOFFSET);
    mpu.setYAccelOffset(YACCELOFFSET);
    mpu.setZAccelOffset(ZACCELOFFSET);
    mpu.setXGyroOffset(XGYRO_OFFSET);
    mpu.setYGyroOffset(YGYRO_OFFSET);
    mpu.setZGyroOffset(ZGYRO_OFFSET);

  if (devStatus == 0) {
  // Calibration Time: generate offsets and calibrate our MPU6050
    mpu.CalibrateAccel(6);
    mpu.CalibrateGyro(6);
    Serial.println();
    mpu.PrintActiveOffsets();
    // turn on the DMP, now that it's ready
    Serial.println(F("Enabling Digital Motion Processor (DMP). Standby..."));
    mpu.setDMPEnabled(true);

    // enable Arduino interrupt detection
    Serial.print(F("Enabling interrupt detection (Arduino external interrupt "));
    Serial.print(digitalPinToInterrupt(INTERRUPT_PIN));
    Serial.println(F(")..."));
    attachInterrupt(digitalPinToInterrupt(INTERRUPT_PIN), dmpDataReady, RISING);
    mpuIntStatus = mpu.getIntStatus();

    // set our DMP Ready flag so the flightControl() function knows it's okay to use it
    Serial.println(F("DMP Calibration complete!"));
    dmpReady = true;

    // get expected DMP packet size for later comparison
    packetSize = mpu.dmpGetFIFOPacketSize();
  } else {
    // ERROR!
    // 1 = initial memory load failed
    // 2 = DMP configuration updates failed
    // (if it's going to break, usually the code will be 1)
    Serial.print(F("DMP Initialization failed (code "));
    Serial.print(devStatus);
    Serial.println(F(")"));
    launchState = "ERROR";
  }

  delay(2000);

  blep(BUZZER_PIN, 523, 50);
  
  if (launchState != "ERROR") {
    Serial.println();Serial.println();
    Serial.println("Here's a little bit of data!");
    for (int i = 0; i < 20; i++) {
      if (mpu.dmpGetCurrentFIFOPacket(fifoBuffer)) {
        mpu.dmpGetQuaternion(&q, fifoBuffer);
        mpu.dmpGetGravity(&gravity, &q);
        mpu.dmpGetYawPitchRoll(ypr, &q, &gravity);
        mpu.dmpGetAccel(&aa, fifoBuffer);
        mpu.dmpGetLinearAccel(&aaReal, &aa, &gravity);
      }
      delay(10);
      Serial.print("a/g:\t");
      Serial.print(aaReal.x); Serial.print("\t");
      Serial.print(aaReal.y); Serial.print("\t");
      Serial.print(aaReal.z); Serial.print("\t");
      Serial.print(ypr[0]); Serial.print("\t");
      Serial.print(ypr[1]); Serial.print("\t");
      Serial.println(ypr[2]);
    }
    Serial.println();Serial.println();
  }

  delay(2000);
  
  if (DEFLECTION_TEST == "ACTIVE") {
    Serial.println("Now let's test the fins! Connecting to servos to perform Deflection Test, standby...");
    Serial.println();Serial.println();
    deflectionTest();
  }


  blep(BUZZER_PIN, 523, 50);

  if (launchState != "ERROR") {

    String readyMsg = "Flight Computer is Armed and Ready!";
    char rMessage[200];
    int r = 0;
    while((r<200)) {
      rMessage[r]=readyMsg[r];  
      r++;
    }

    if (STARTLAUNCHSTATE != "DEBUG") {
      launchState = "ARMED";
    } else {
      launchState = STARTLAUNCHSTATE;
    }

    Serial.println();
    Serial.print("Flight Computer Status: ");Serial.println(launchState);
    
    delay(1000);

    Serial.println();Serial.println();
    Serial.println(rMessage);
    Serial.println();Serial.println();

    /**********************************
     * ? Send status update over LoRa ?
     * ! REMOVE WHEN TESTING OFFLINE  !
     **********************************/
    if (TELEMETRY == "ACTIVE") {
      rf95.send((uint8_t *)rMessage, 200);
      delay(10);
      rf95.waitPacketSent();
    }
  }

  blep(BUZZER_PIN, 1760, 500);
  
  delay(1000);
  
  // Prepare Pyro Channel 1 (PYRO_1) for chute charge ignition
   if (PYRO1) {
    pinMode(PYRO_1, OUTPUT);
    digitalWrite(PYRO_1, LOW);
   }

  // readyForLaunch();
}

/********************************************************************************************************************************************************************/
/********************************************************************************************************************************************************************/
/********************************************************************* Sensor Data Assimilation *********************************************************************/
/********************************************************************************************************************************************************************/
/********************************************************************************************************************************************************************/


// XYZ Position Calculations
float calculateXDisplacement(float accelX) {
  // Filter noise from accelerometer
  float filteredX = xKalmanFilter.updateEstimate(accelX);
//  xVel = xVel + (filteredX * time);
//  xPos = calculateDistance(xPos, xVel, filteredX, time);
  // Calculate rate of change in acceleration
//  float dxAccel = (filteredX - xAccel);
//  if (dxAccel == 0) return xPos; // If the acceleration hasn't changed, then we are not moving
//
//  dxAccel = dxAccel * 9.8; // Cancel out gravity?
//
//  xPos = 0.5 * dxAccel * sq(time);

  xPos = filteredX;
  

  return xPos;
}

float calculateYDisplacement(float accelY) {
  yPos = yKalmanFilter.updateEstimate(accelY);
//  yPos = calculateDistance(yPos, accelY, millis());
  return yPos;
}

float calculateZDisplacement(float accelZ) {
  zPos = zKalmanFilter.updateEstimate(accelZ);
//  zPos = calculateDistance(zPos, accelZ, millis());
  return zPos;
}

float calculateAltitude(float alt, float accel) {
  // Create a new kalman filter
  SimpleKalmanFilter altitudeKalmanFilter(1, 1, 0.01);
  // Set altitude to accelerometer 
  //  float altitude = bme.seaLevelForAltitude(accel, (bme.readPressure() / 100.0F));
  float altitude = altitudeKalmanFilter.updateEstimate(alt);
  return altitude;
}

float calculateDistance(float pos, float velocity, float accel, float t) {
  // Using the second integration of the acceleration function:
  float distance = pos + (velocity * time) + (0.5 * accel * sq(time));
  return distance;
}

void getVehicleAltitude() {
  unsigned long missionTime = millis();
  if (missionTime - prevDeployTime >= 3000) {
    prevDeployTime = missionTime;
    altitude = bme.readAltitude(SEALEVELPRESSURE_HPA);
    if (altitude > lastAlt) {
      lastAlt = altitude;
    } else if (altitude < lastAlt && altitude - lastAlt <= -10) {
      apogee = altitude;
      delay(150);
      deploy();
    } 
  }
}

/*********************************************************************************************************************************************************************/
/*********************************************************************************************************************************************************************/
/************************************************************************ Auxillary Functions ************************************************************************/
/*********************************************************************************************************************************************************************/
/*********************************************************************************************************************************************************************/

void blep(uint8_t buzzerPin, int pitch, int length) {
  if (!mute) {
    tone(buzzerPin, pitch);
    digitalWrite(LEDPIN, HIGH);
    delay(length);
    noTone(buzzerPin);
    digitalWrite(LEDPIN, LOW);
  }
}

/***********************************************************************************************/
/*********************************** REACTION CONTROL SYSTEM ***********************************/
/***********************************************************************************************/
void rcs(float *ypr) {
  // Convert Yaw/Pitch/Roll to readable values   
  ypr[0] = ypr[0] * 180 / M_PI;
  ypr[1] = ypr[1] * 180 / M_PI;
  ypr[2] = ypr[2] * 180 / M_PI;

  // Add Yaw/Pitch/Roll values to Kalman Filter(s)
  ypr[0] = yawKalmanFilter.updateEstimate(ypr[0]);
  ypr[1] = pitchKalmanFilter.updateEstimate(ypr[1]);
  ypr[2] = rollKalmanFilter.updateEstimate(ypr[2]);

  {/********************************/}
  {/* !! SOMETHING IS WRONG HERE !!*/}
  {/********************************/}

  // if (launchState == "LIFTOFF" || launchState == "FLIGHT") {
  // Map the values of the MPU6050 sensor from -90 to 90 to values suitable for the servo control from 0 to 180
  int servo0Value = map(ypr[2], -90, 90, 0, 180);
  int servo1Value = map(ypr[2], -90, 90, 0, 180);
  int servo2Value = map(ypr[2], -90, 90, 0, 180);
  int servo3Value = map(ypr[2], -90, 90, 0, 180);

  // Control the servos according to the MPU6050 orientation
  servo0.write(servo0Value);
  servo1.write(servo1Value);
  servo2.write(servo2Value);
  servo3.write(servo3Value);
  // }
}

void deflectionTest() {
  servo0.attach(servo0Pin);
  servo1.attach(servo1Pin);
  servo2.attach(servo2Pin);
  servo3.attach(servo3Pin);
  
  // Test servo functionality
  servo0.write(180);
  servo1.write(-180);
  servo2.write(180);
  servo3.write(-180);
  delay(2000);
  servo0.write(-180);
  servo1.write(180);
  servo2.write(-180);
  servo3.write(180);
  delay(2000);
  servo0.write(90);
  servo1.write(90);
  servo2.write(90);
  servo3.write(90);
  delay(2000);
}

void deploy() {
 chutesFired = true;
 // Fire relay
 digitalWrite(PYRO_1, HIGH);
 delay(1000);
 digitalWrite(PYRO_1, LOW);
 delay(100);
}

void touchdown() {
  altitude = bme.readAltitude(SEALEVELPRESSURE_HPA);
 if (altitude - lastAlt == 0) {
    landed = true;
    launchState = "TOUCHDOWN";
  }
}
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

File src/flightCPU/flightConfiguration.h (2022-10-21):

#define debugState "ON"
#define mute false

// Current Atmospheric Pressure (UPDATE BEFORE FLIGHT)
#define SEALEVELPRESSURE_HPA (1015.2)

#define XACCELOFFSET 1381
#define YACCELOFFSET -399
#define ZACCELOFFSET 3855
#define XGYRO_OFFSET 50
#define YGYRO_OFFSET 98
#define ZGYRO_OFFSET 21

#define TELEMETRY "INACTIVE"
#define DEFLECTION_TEST "ACTIVE"

#define PYRO1 false

#define STARTLAUNCHSTATE ""

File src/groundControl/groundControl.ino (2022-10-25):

#include "Wire.h"
#include <SPI.h>
#include <RH_RF95.h>
#include "config.h"

// Singleton instance of the radio driver
RH_RF95 rf95(RFM95_CS, RFM95_INT);

int16_t packetnum = 0;  // packet counter, we increment per transmission

String telemStatus = "OFF";

/*****************************************************************************************************************************************************************************
 *********************************************************************************   Setup   *********************************************************************************
 *****************************************************************************************************************************************************************************/

void setup() {
  /*   Prep RMF95 for flight   */
  if (TELEMETRY == "ACTIVE") {
    pinMode(RFM95_RST, OUTPUT);
    digitalWrite(RFM95_RST, HIGH);
  }

  Serial.begin(115200);
  
  // Wait for serial to be available if board is in 'DEBUG' mode
  if (debugState == "ON") {
    while (!Serial) {
    }
  }

  // Run pre-flight check
  preCheck();
}


// !WIP - Output data to Serial Studio as:
// `/*BLEP,x,x,x,x,x,...x*/` string 


/**
 * TODO:--
 * * Connect LoRa featherwing and get RF breakout working
 * * Create direct, one-to-one RF communication between ground and blep
 * * Install additional components (buzzer, LED, relayWing, etc)
 * * Design launch pad
 * * Wire new (cool) flip switch to prevent accidental launch
 * * Format serial output for SerialStudio collection and analysis
 * * Create a countdown loop that can be cancelled in case of emergency on the pad
 * * 
 */

/*****************************************************************************************************************************************************************************
 ********************************************************************************* Main loop *********************************************************************************
 *****************************************************************************************************************************************************************************/
void loop() {
  /**
   * @note - The flight CPU should have the following "commands", receivable via 900mHz radio from the launch pad controller
   * 
   * @param - STARTUP
   * @param - TELEM
   * @param - ARMED
   * @param - IGNITION / LAUNCH
   * @param - DEPLOY / CHUTE
   * @param - REBOOT
   */
    digitalWrite(LEDPIN, HIGH);
    delay(50);
    digitalWrite(LEDPIN, LOW);
    delay(500);
    Serial.println("Waiting for data...");
    delay(1000);

    if (TELEMETRY == "ACTIVE") {
      if (rf95.available()) {
        // Should be a message for us now   
        uint8_t buf[RH_RF95_MAX_MESSAGE_LEN];
        uint8_t len = sizeof(buf);
        if (rf95.recv(buf, &len)) {
          if (!len) return;
          buf[len] = 0;
        Serial.print("Received [");
        Serial.print(len);
        Serial.print("]: ");
        Serial.print("RSSI: ");
        Serial.println(rf95.lastRssi(), DEC);
          Serial.println((char*)buf);
        } else {
          Serial.println("Receive failed");
        }
      }
    } else {
      Serial.println('Radio module disabled. Connect the antenna and turn on telemetry in the config.h file.');
    }
}

void preCheck() {
  Serial.println();Serial.println();
  Serial.println("Beginning Pre-Flight Software check.");
  Serial.println();Serial.println();
  delay(2000);

  telemStatus = "STARTUP";
  Serial.println();
  Serial.print("Ground Control Computer Status: ");Serial.println(telemStatus);

  pinMode(LEDPIN, OUTPUT);

  if (!mute) {
    // Play bootup sequence sound
    for (unsigned int i = 0; i < numTones; i++) {
      tone(A1, tones[i]);
      delay(50);
    }
    noTone(A1);
  }

  delay(2000);  // time to get serial running

/*********************************************************
 * Send data to the flight computer to see if it's awake. *
 * Check if the flight computer responded.                *
 *********************************************************/

  // <Some RF95 code>
  Serial.println("Blep Flight Computer Online!");
  telemStatus = "TELEM"; // This means we have a direct radio connection to the flight computer -- congrats!

}

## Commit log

2021-10-25 Pushing current working code to repo
2021-10-25 Added tentative airframe schematics
2021-10-31 Cleaned ground control code
2022-09-17 Updated test code, and fixed code structure. Prepping code for major update
    [flightCPU.ino]
2022-09-26 Improved IMU data collection, uploaded schematics and updated readme
    [Avionics Payload Mount.dwg]
2022-09-29 Added new PCB schematics
    [FlightComputer.brd, FlightComputer.dxf, FlightComputer.sch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]
2022-10-04 Added missing commit from minor/v1.3 to master
    [Avionics Payload Mount.dwg, FlightComputer v6.step]
2022-10-19 Created header files for simplicity and abstracted code for cleanliness
    [Avionics Payload Mount.dwg, FlightComputer.brd, FlightComputer.sch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]

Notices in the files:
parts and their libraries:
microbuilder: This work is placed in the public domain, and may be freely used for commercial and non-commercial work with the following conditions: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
